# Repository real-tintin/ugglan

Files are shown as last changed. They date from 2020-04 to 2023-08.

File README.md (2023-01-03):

# Ugglan
Ugglan (owl in Swedish) is a hobby drone project. Making use of the
Raspberry Pi Zero 2 W (amongst other things).

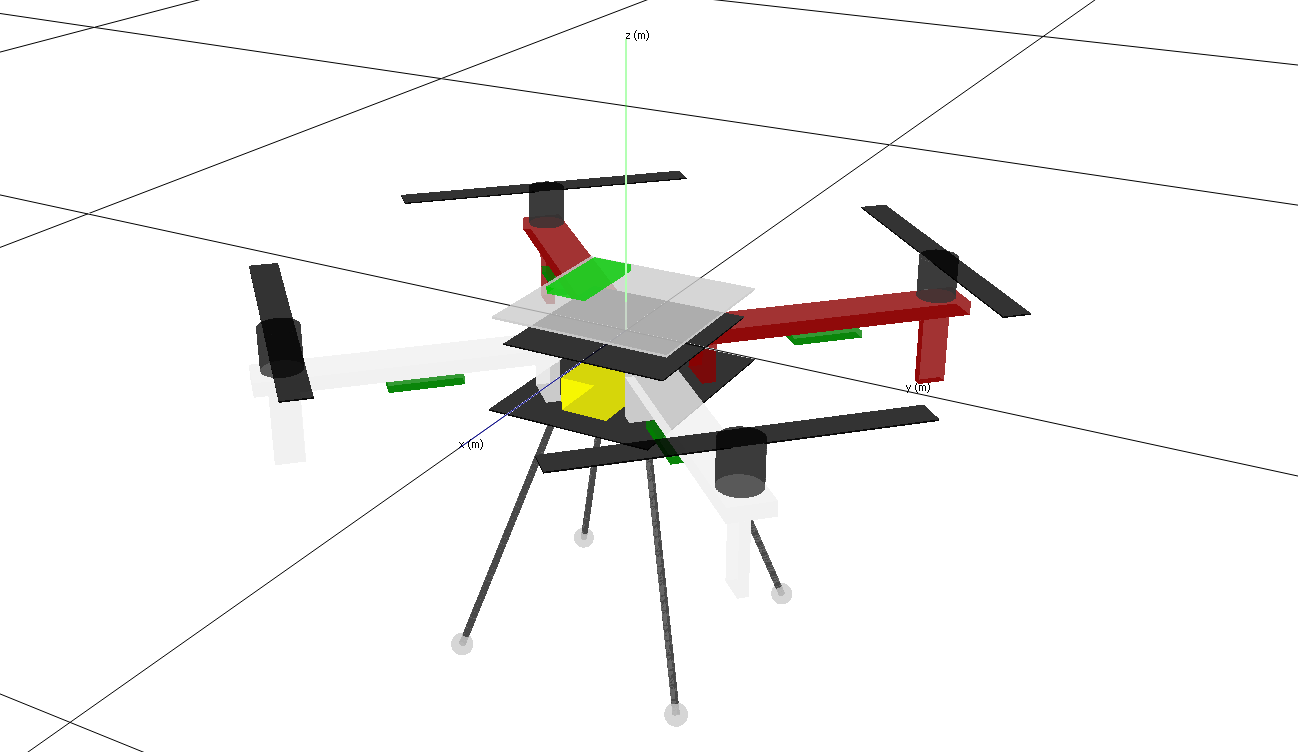
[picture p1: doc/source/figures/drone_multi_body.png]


The project serves as a learning platform for the author himself and
is quite broad, containing everything from assembler to docker. It
also contains some multi body modelling and simulation as well as
state space estimation and control.

## Setup

### Prerequisites
* python >=3.9
* docker
* make

Run the setup script in the root.

```bash
source ./setup.sh
```

## Documentation
[Sphinx](https://www.sphinx-doc.org/en/master/) is used for the generation
of the documentation.

### Build
The documentation is build using `make`.

```bash
make -C ./doc
```

The generated html documentation is found under *./doc/build*.

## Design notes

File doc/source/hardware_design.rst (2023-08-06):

Hardware Design
*****************
.. _ugglan_in_person:
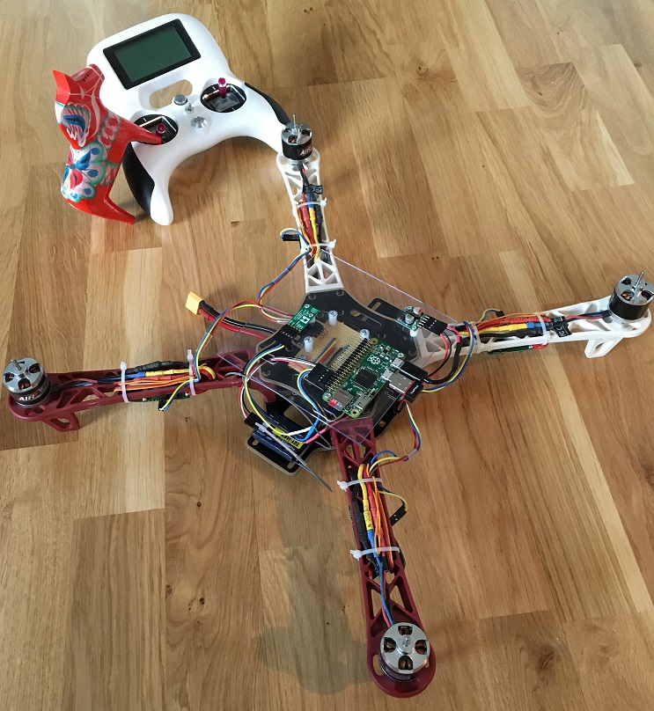
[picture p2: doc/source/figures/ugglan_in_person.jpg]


    Ugglan in person.

Components
==============
The drone hardware components are is listed below

* Raspberry Pi Zero 2 W
* Diatone Q450 with PCB
* Pololu AltIMU-10 v4
* Afro ESC 20 A
* Turnigy Evolution Digital AFHDS 2A RC transmitter & controller
* TGY-iA6C RC receiver
* ZIPPY Compact 3300mAh 3S (or similar)
* DC-DC step down voltage regulator 5V
* T-MOTOR MN2212-V2.0 Brushless Motor (KV920)
* T-MOTOR T9545-A Propeller 9.5x4.5

In addition, miscellaneous self manufactured components such as a cut plexiglas
are used for mounting, see :numref:`ugglan_in_person`.

.. _devices_and_busses:

Devices & Busses
==================
The IMU's and ESC's are communicating with the Pi over i2c. The IMU can run at 400 kHz (fast mode)
and is using the built-in HW. But, the ESC's only run stable at 100 kHz (normal mode) and are
therefore using a SW implementation (i2c-gpio overlay, bit-banging over GPIO 23-24). The RC receiver
is communicating over UART, a serial connection. See overview in :numref:`connected_busses`.

.. _connected_busses:
.. mermaid::
    :caption: Overview of the hardware devices connected to the Pi Zero 2 W and their respective protocols.

    graph TD
        Esc_i -- i2c read 100 kHz --> Raspi
        Raspi -- i2c write 100 kHz --> Esc_i
        Imu_i -- i2c read 400 kHz --> Raspi
        RcReceiver -- uart read 115200 bps --> Raspi

Wiring
==================
.. _wiring_diagram:


    Wiring diagram.

Single core vs. Multi core
============================
During the project, the Raspberry Pi Zero single core processor was upgraded to a 2 W multi core
processor. As the application is utilizing threading, it was interesting to compare the
application performance between the two.

In :numref:`task_exec_rate_single_core` and :numref:`task_exec_rate_multi_core` the task execution
rates in time is shown. As one can see, the execution rates on the multi core processor are much smoother.

.. _task_exec_rate_single_core:


    Task execution rates on the single core Raspberry Pi Zero.

.. _task_exec_rate_multi_core:


    Task execution rates on the multi core Raspberry Pi Zero 2 W.

Vibrations & Attenuation
=========================
The rotating motor with propeller is a source for mechanical vibrations. Un-balanced motors and propellers
will induce vibrations and can cause issue during state estimation e.g., the vibration will propagate thru
the frame to the IMU and cause un-wanted noise.

Motor & Propeller Balancing
^^^^^^^^^^^^^^^^^^^^^^^^^^^^
To reduce vibrations the motor and propeller need to be balanced. To analyze and balance them the IMU acceleration
can be studied. In :numref:`vib_analysis_prop_balancing` the IMU acceleration in time, its variance and psd (power
spectral density) is shown for different runs where a pice of tape is positioned at different locations on a propeller.

.. _vib_analysis_prop_balancing:


    Each chunk corresponds to a separate run of the motors where the pice of tape is relocated. Note,
    chunk 0 is without any tape, chunk 1-3 is tape on one blade and chunk 4-6 on the other blade.

It can be seen that applying tape on a certain location can significantly reduce vibrations i.e., becoming
"better" balanced.

Also note the frequency components of the psd. The content at ~20 Hz could correspond to the frequency of
the motors but folded (due to aliasing as the sample rate 100/2 Hz < 81 Hz, hence at folded at 19 Hz).

Vibration Dampers
^^^^^^^^^^^^^^^^^^
The vibrations experienced by the IMU can be further reduced by installing vibrations dampers between
the frame and the custom mounting plate, see :numref:`ugglan_in_person`.

Different rubber dampers were tested (varying stiffness, mass and size), see :numref:`table_vibration_dampers`
for results.

.. _table_vibration_dampers:

.. table:: * See `data sheet <https://www.tme.eu/Document/3783353bba387d7e09757c85b47027b3/DVA1-3-EN.pdf>`_ for details.

    ====================    ================    ========    ===================     ===================
    Name*                   Stiffness [N/mm]    Mass [g]    Eigenfrequency [Hz]     Variance [m^2/s^4]
    ====================    ================    ========    ===================     ===================
    DVA.1-15-15-M4-10-55    39                  10          314                     1.12
    DVA.1-15-15-M4-10-70    118                 10          537                     0.85
    DVA.1-15-20-M4-10-40    20                  12          206                     2.40
    DVA.1-15-20-M4-10-55    25                  12          230                     1.30
    ====================    ================    ========    ===================     ===================

The above results are rather concise - increasing eigenfrequency will result in less experienced vibrations
by the IMU. This is most likely due the fact that the plate is vibrating about the motor rotational frequency
(~160 Hz). Hence, it would be interesting to test a damper with an eigenfrequency << 160 Hz.

Note, the eigenfrequency is estimated by assuming a classic second order mass-spring system i.e.,
:math:`f_n = \tfrac{1}{2\pi}\sqrt{\tfrac{k}{m}}` (SI-units).

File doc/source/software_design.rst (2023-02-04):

Software Design
*****************

Tasks
=================
The drone's top level software design can be seen as a task manager, (asynchronous
and synchronous) solving the producer and consumer problem. Where the producers are
the sensors (IMU, ESC etc.). And where the control loop, data logging etc. are
the consumers, see :numref:`drone_sw_design`.

.. _drone_sw_design:
.. mermaid::
    :caption: Overview of the drone software design. Tasks are stadium-shaped nodes.

    graph LR
        ImuAccMag([ImuAccMag])
        ImuGyro([ImuGyro])
        ImuPres([ImuPres])

        EscRead([EscRead])
        EscWrite([EscWrite])

        RcReceiver([RcReceiver])

        StateEst([StateEst])
        StateCtrl([StateCtrl])

        DataLogger([DataLogger])

        DataLogQueue[(DataLogQueue)]

        ImuAccMag -- push 100 Hz --> DataLogQueue
        ImuGyro -- push 100 Hz --> DataLogQueue
        ImuPres -- push 10 Hz --> DataLogQueue
        EscRead -- push 1 Hz --> DataLogQueue
        RcReceiver -- push 100 Hz --> DataLogQueue

        DataLogQueue -- last value 100 Hz --> StateEst
        DataLogQueue -- last value 100 Hz --> StateCtrl
        DataLogQueue -- last value 100 Hz --> EscWrite
        DataLogQueue -- last value 100 Hz --> StreamerServer
        DataLogQueue -- pack 10 Hz --> DataLogger

        subgraph Producers
        ImuAccMag
        ImuGyro
        ImuPres
        EscRead
        RcReceiver
        end

        subgraph Consumers
        StateEst
        StateCtrl
        EscWrite
        DataLogger
        StreamerServer
        end

As one can see, the ``DataLogQueue`` maintains a thread safe queue for the producers to
push to and the ``DataLogger`` to pack (pop until empty) from. But it also stores the last
(pushed) sample for consumers to use e.g., the ``StateEst`` which runs at a constant sample
rate i.e., to simplify the signal processing. Note, other tasks than producers may populate
the queue e.g., estimated states which are used by the ``StateCtrl`` or for offline
tuning of control laws.

.. _data_logging:

Data Logging
=================
The ``DataLogger`` handles the data serialization of signals e.g., the IMU acceleration
which is continuously written to disk. It consists of a **HEADER** section - a json string,
describing the content of the second **DATA PACKAGES** section. See :numref:`data_log_protocol`
for an illustration of the data-log protocol.

.. _data_log_protocol:


    The data logging protocol. The **SIGNAL ID** is an unique identifier for each signal/package
    and of type ``uint16``. The **REL TIMESTAMP** is the relative timestamp in ms
    between each **PACKAGE** and of type ``uint8``.

The json-file is compressed using gzip (and base64 encoded) to save space. See example
header below.

.. code-block:: json

    {
        "start_time": "1990-08-30T22:52:50Z",
        "types": {
            "0": "UINT8",
            "1": "UINT16",
            "2": "UINT32",
            "3": "SINT8",
            "4": "SINT16",
            "5": "SINT32",
            "6": "FLOAT",
            "7": "DOUBLE"
        },
        "groups": {
            "0": "IMU",
            "1": "ESC"
        },
        "signals": {
            "0": {
                "name": "AccelerationX",
                "group": 0,
                "type": 7
            },
            "1": {
                "name": "Status0",
                "group": 1,
                "type": 0
            }
        }
    }

State Machine
=================

User Operator
---------------

.. mermaid::
    :caption: User operation of ESC's. LS: Left Switch. MS: Middle Switch.

    stateDiagram

        [*] --> Sound
        Sound --> Disarmed
        Disarmed --> Armed: LS Mid
        Armed --> Disarmed: LS Hi
        Armed --> Alive: LS Lo
        Alive --> Armed: LS Mid
        Disarmed --> [*]: MS Lo

Wireless Streaming
===================
There exists support for wireless data streaming from the drone. The streaming is build
on top of the open-source message library `ZeroMQ <https://zeromq.org>`_. In
:numref:`wireless_streaming_seq_diagram` the communication sequence between the client
(e.g., Laptop) and the server (drone) is illustrated.

.. _wireless_streaming_seq_diagram:
.. mermaid::
    :caption: Communication sequence between the client and the server. Note, only a subset of all available requests are shown.

    sequenceDiagram
        Client->>Server: Request[method: Get_DataLogMetadata<0>, data:{}]
        Server-->>Client: Response[code: Ok<0>, data:<DataLogMetadata as JSON>]
        Client->>Server: Request[method: Set_SelectedDataLogSignals<4>, data:[0,1,2,3]]
        Server-->>Client: Response[code: Ok<0>, data:{}]
        Client->>Server: Request[method: Set_StartStream<2>, data:{}]
        Server-->>Client: Response[code: Ok<0>, data:{}]
        loop
            Server-->>Client: Pushing[Selected data log signal package]
        end
        Client->>Server: Request[method: Set_StopStream<3>, data:{}]
        Server-->>Client: Response[code: Ok, data:{}]

The requests/responses are sent on a socket using the ``REQUEST-REPLY`` pattern, while
the actual selected data log signal bytes are sent on separate socket using the ``PUSH-PULL``
pattern. This to improve performance.

The data sent back and forth via requests/responses are JSON, while the data log signal
package is packed as following::

    <ABS_TIMESTAMP><DATA_LOG_SIGNALS>

and the data log signals are packed as::

    <ID_0><BYTES_0>...<ID_N><BYTES_N>

Note, they are packed somewhat differently compared to the data log signals in
:ref:`data_logging`. This since we can't really unsure that relative timestamps will be
continuous between sent packages.

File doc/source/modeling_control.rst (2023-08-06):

Modeling & Control
*******************
.. _drone_multi_body:


    Multi body analysis of the drone. The 3d model is generated by using
    ``PyQtGraph`` (opengl backend).

Before moving on, note that some in-depth parts of the modeling, state estimation
and Control are not covered in this document, for details see the arthur's master
thesis `Design-Modeling-and-Control-of-an-Octocopter`_.

.. _Design-Modeling-and-Control-of-an-Octocopter: http://www.diva-portal.org/smash/get/diva2:857660/FULLTEXT01.pdf

Nomenclature
===================
:math:`_{I}` Inertial reference frame

:math:`_{B}` Body reference frame

:math:`\tau` Time-constant

:math:`M` Torque

:math:`F` Force

Inertia
===================

Multi Body Modeling
---------------------
Using multi body analysis of the drone and its components, the total drone
(mass and moments) inertia is estimated, see :numref:`drone_multi_body`.
This results in the following inertia estimates

.. math::

    I_{est} =
    \begin{bmatrix}
        0.013 & 0 & 0 \\
        0 & 0.013 & 0 \\
        0 & 0 & 0.024
    \end{bmatrix} \text{kgm}^2

and :math:`m_{est}=1.027` kg. For comparison, the measured weight is :math:`m_{meas}=1.071` kg.
Also its center of mass w.r.t the top frame is located at :math:`CM_{est}=[0, -0.001, -0.011]` m.
Hence, a rather good weight distribution.

The Pendulum Experiment
------------------------
In `Design-Modeling-and-Control-of-an-Octocopter`_ (Section 2.2) an experiment is proposed for
estimation the rotational moment of inertia. This by measuring the period time of a rigid body
rotating about an axis suspended by two strings i.e., bifilar pendulum.

Without going into the details, :math:`I_{zz}` was estimated by suspending the drone by two
strings apart :math:`D=0.46` m with length :math:`L=2.16` m, see :numref:`pendulum_experiment`.

.. _pendulum_experiment:
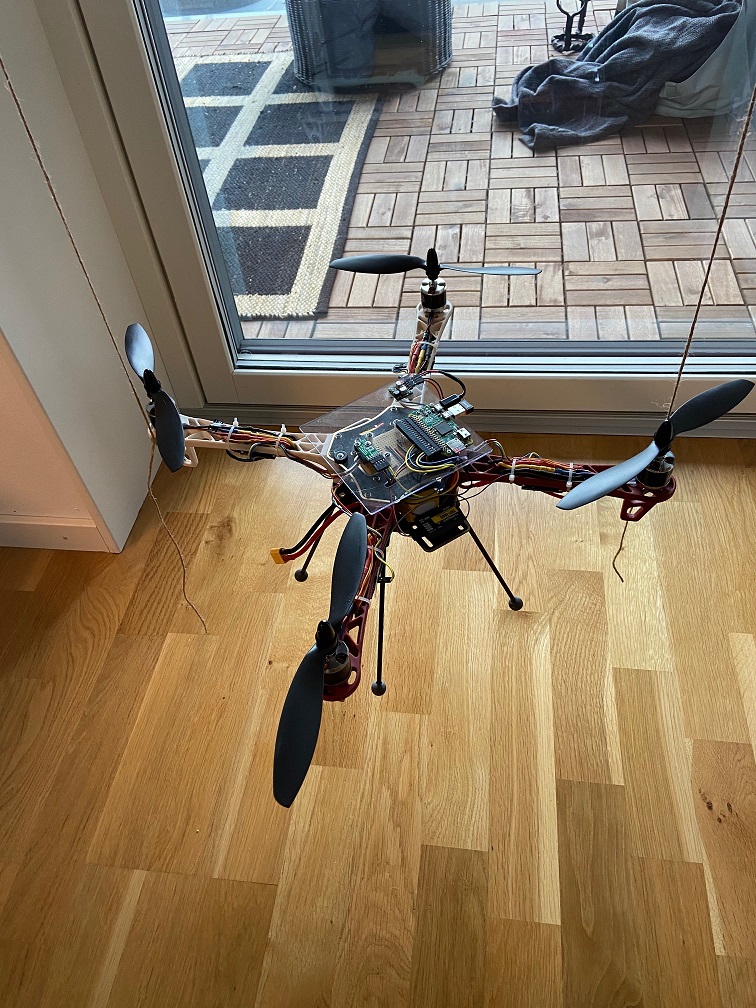
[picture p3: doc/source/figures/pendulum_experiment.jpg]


    Ugglan suspended by two strings - help?!

In total 10 measurements where made of the number of periods and the total time, listed in
:numref:`table_pendulum`.

.. _table_pendulum:

.. table:: :math:`N` number of periods and :math:`t` total time.

    =======  =======
    N        t [s]
    =======  =======
    10       19.3
    10       19.4
    15       29.2
    15       29.1
    20       39.0
    20       38.8
    25       48.2
    25       48.2
    30       58.1
    30       57.8
    =======  =======

Computing the mean period yields :math:`T=1.94` s. This in terms results in
:math:`I_{zz}=0.025 \text{ kgm}^2`. This can be seen as an validation of the estimation
from the multi body modeling.

Motor Dynamics
================
The motor dynamics, :math:`u_{M_i}\rightarrow\omega_{M_iz}` are modelled as a simple first order
LTL system (low-pass filter)

.. math::

    \Omega_{M_iz}(s) = \frac{1}{\tau_M s + 1}U_{M_i}(s)

where :math:`\tau_M` is the motor time constant. The time constant can be estimated by analyzing
the systems step response. By assuming :math:`\omega_{M_i}(0) = u_0` and
:math:`\omega_{M_i}(\infty) = u_\infty`, before and after the step response as settled, one gets

.. math::

    \omega_{M_i}(t) = u_\infty + (u_0 - u_\infty) e^{\frac{-t}{\tau_M}}

which can be re-written as

.. math::

    \ln\left(\frac{u_\infty - u_0}{u_\infty - \omega_{M_i}(t)}\right) = \tau_M^{-1} t

assuming :math:`u_\infty > u_0`. By then measuring :math:`\omega_{M_i}` and :math:`t` one can
estimate :math:`\tau_M` by using least squares regression. Note the data points for the regression
should be selected such that the problem is well conditioned i.e.,
:math:`\omega_{M_i} \lesssim u_\infty`.

In :numref:`tau_motor_dynamics` the time constant is estimated. One can see that it does vary
and decrease with an increasing :math:`u_0`, introducing a non-linearity. Moreover,
:math:`\tau_M` varies for positive and negative steps.

The seen effects have to be neglected to keep linearity. Therefore, the resulting time constant
is given by the mean of the steps responses where :math:`\omega_M \in [400, 800]` i.e., within
normal operating conditions. This gives :math:`\tau_M = 0.08`.

.. _tau_motor_dynamics:


    Positive and negative motor step responses (with mounted propeller). The time constant
    is estimated for each step using MLSE.

On a further note. The approximation of using a first order low pass filter is fine. But from the
figure it becomes clear that better approximations of higher order exist. An improvement would
be to empirical derive such a system - by using system identification.

Linearized State Space
=======================
The same linearized (SIMO) state-space representation as derived in
`Design-Modeling-and-Control-of-an-Octocopter`_ (Section 3.7) is used i.e.,

.. math::

    \mathbf{\dot{x}_i} &= \mathbf{A_i x_i} + \mathbf{B_i} u_i \\
    \mathbf{y_i} &= \mathbf{C_i x_i} + \mathbf{D_i} u_i, i = 1,2,...,6

where :math:`\mathbf{x_i}\in\mathbb{R}^3`, :math:`\mathbf{y_i}\in\mathbb{R}^2` and

.. math::
    :label: state_space_matrices

    \mathbf{A_i}=
    \begin{bmatrix}
        0 & 1 & 0 \\
        0 & 0 & 1 \\
        0 & 0 & -\tfrac{1}{\tau_M}
    \end{bmatrix},
    \mathbf{B_i}=
    \begin{bmatrix}
        0 \\
        0 \\
        \tfrac{c_i}{\tau_M}
    \end{bmatrix},
    \mathbf{C_i}=
    \begin{bmatrix}
        1 & 0 & 0 \\
        0 & 1 & 0 \\
        0 & 0 & 1
    \end{bmatrix},
    \mathbf{D_i}= 0.

Here :math:`\mathbf{c} = [\tfrac{1}{m}, \tfrac{1}{m}, \tfrac{1}{m}, \tfrac{1}{I_{xx}},
\tfrac{1}{I_{yy}}, \tfrac{1}{I_{zz}}]`. For instance :math:`i = 4` corresponds to the
state-space representation in roll

.. math::

    \mathbf{x_4}=
    \begin{bmatrix}
        \phi \\
        \dot\phi \\
        \ddot\phi \\
    \end{bmatrix},
    u_4=u_\phi,
    c_4=\tfrac{1}{I_{xx}}.

Note, the final state e.g., :math:`\ddot\phi` is estimated using a Kalman filter,
see :ref:`attitude-estimation`. This differs from the master thesis, where it was
estimated using a reduced observer.

State Estimation
=================

.. _attitude-estimation:

Attitude Estimation
--------------------
For attitude control, the Euler angles :math:`\eta = [\phi, \theta, \psi]` and their respective
time derivatives :math:`\dot{\eta}` (angular rates) and :math:`\ddot{\eta}` (angular accelerations)
are needed.

Geometry of IMU
^^^^^^^^^^^^^^^^
The euler angles can directly be computed from the IMU's accelerometer and magnetometer using
the geometrical relationships

.. math::

    \phi_{acc} &= \text{atan2}(-a_{By}, -a_{Bz}) \\
    \theta_{acc} &= \text{atan2}(a_{Bx}, \sqrt{a_{By}^2 + a_{Bz}^2}) \\
    \psi_{mag} &= \text{atan2}(-B_{Iy}, B_{Ix})

where

.. math::

    B_{Ix} &= B_{Bx}\cos(\theta) + B_{By}\sin(\phi)\sin(\theta) + B_{Bz}\sin(\theta)\cos(\phi) \\
    B_{Iy} &= B_{By}\cos(\phi) - B_{Bz}\sin(\phi)

and :math:`a_B` is the acceleration and :math:`B_B` is the earths magnetic field supplied by the
IMU in the body frame. Where :math:`B_{Ix}` and :math:`B_{Iy}` are the magnetic fields in the
inertial frame.

However, the estimates are noisy (see :numref:`ang_est`) and need to be enhanced
e.g., by filtering.

Kalman Filter
^^^^^^^^^^^^^^
A full state attitude estimation can be accomplished by using a Kalman filter (MLSE filter which assumes
linearity and Gaussian noise) see e.g., `Wikipedia <https://en.wikipedia.org/wiki/Kalman_filter>`_ for
details. This is a rather common approach for attitude estimation given the IMU outputs. So, without
going into the details, the time discretized state space model in this case becomes

.. math::
    :label: kalman_filter_ss

    \mathbf{F}=
    \begin{bmatrix}
        1 & \Delta t & \tfrac{\Delta t^2}{2} \\
        0 & 1 & \Delta t \\
        0 & 0 & 1
    \end{bmatrix},
    \mathbf{B}= 0,
    \mathbf{H}=
    \begin{bmatrix}
        1 & 0 & 0 \\
        0 & 1 & 0
    \end{bmatrix}

with the selected covariance matrices

.. math::
    :label: kalman_filter_cov

    \mathbf{Q}= \kappa_{Q}
    \begin{bmatrix}
        \tfrac{\Delta t^4}{4} & \tfrac{\Delta t^3}{2} & \tfrac{\Delta t^2}{2} \\
        \tfrac{\Delta t^3}{2} & \Delta t^2 & \Delta t \\
        \tfrac{\Delta t^2}{2} & \Delta t & 1
    \end{bmatrix},
    \mathbf{R}=
    \begin{bmatrix}
        \kappa_{R_0} & 0 \\
        0 & \kappa_{R_1}
    \end{bmatrix},
    \mathbf{P}_0= I.

The :math:`\kappa` are tunable parameters of the filter.

See :ref:`estimator-performance` for the final performance
and comparison w.r.t to other filtering methods.

Complementary filter
^^^^^^^^^^^^^^^^^^^^^
Another method to improve the (angle only) estimates is to use a first order complementary filter -
fusing the accelerometer angles with the integrated gyro estimates (see
`IMU Data Fusing <http://www.olliw.eu/2013/imu-data-fusing/>`_)

.. math::

    \tilde{\phi}^{k} &= \text{cf}(\phi_{acc}^k, \dot{\phi}_{gyro}^k, \tilde{\phi}^{k-1}, \tau_{\phi}) \\
    \tilde{\theta}^{k} &= \text{cf}(\theta_{acc}^k, \dot{\theta}_{gyro}^k, \tilde{\theta}^{k-1}, \tau_{\theta}) \\
    \tilde{\psi}^{k} &= \text{cf}(\psi_{mag}^k, \dot{\psi}_{gyro}^k, \tilde{\psi}^{k-1}, \tau_{\psi})

where

.. math::

    y^{k} &= \text{cf}(u^k, \dot{u}^k, y^{k-1}, \tau) \\
            &= \alpha(y^{k-1} + \dot{u}^k\Delta t) + (1-\alpha)u^k

where :math:`\alpha = \tfrac{\tau}{\tau + \Delta t}` and :math:`\tau` is the cut-off frequency
(:math:`\tau = \tfrac{1}{2 \pi f_c}`).

.. _estimator-performance:

Estimator Performance
^^^^^^^^^^^^^^^^^^^^^^
In :numref:`ang_est` - :numref:`ang_acc_est` the final performance of the attitude
estimation is show for different estimators.

.. _ang_est:


    Angle estimation using the IMU (accelerometer + magnetometer), integrated gyro,
    complementary filter and the Kalman filter.

.. _ang_rate_est:


    Angular rate estimation using the gyro output and the Kalman filter.

.. _ang_acc_est:


    Angular acceleration estimation using the derivative of the gyro (w/o a LP-filter)
    and the Kalman filter.

Implementation Notes
^^^^^^^^^^^^^^^^^^^^^

Kalman Filter
"""""""""""""""""
In order to solve for the optimal Kalman gain, matrix operations (e.g., inverse) have
to be performed. For this `Eigen <https://eigen.tuxfamily.org/>`_ is used.

Range Limit
"""""""""""""""
The estimates need to be range limited i.e., modulo of the euler angles e.g.,
:math:`\theta \in [-\pi, \pi]`.

Accelerometer Static Errors
"""""""""""""""""""""""""""
The accelerometer output is typically polluted with static errors which need
to be compensated for. These errors can split into scaling errors, misalignment
errors and biases (offset errors). The relation between the raw sensor output
:math:`\tilde{V}` and the true (compensated) output :math:`V` can be expressed
as following

.. math::

    \underbrace{
        \begin{bmatrix}
            x \\
            y \\
            z
        \end{bmatrix}
    }_V =
    \underbrace{
        \begin{bmatrix}
            s_x & 0 & 0 \\
            0 & s_y & 0 \\
            0 & 0 & s_z
        \end{bmatrix}
    }_S
    \underbrace{
        \begin{bmatrix}
                1 & m_{xy} & m_{xz} \\
                m_{yx} & 1 & m_{yz} \\
                m_{zx} & m_{zy} & 1
        \end{bmatrix}
    }_M
    \underbrace{
        \begin{bmatrix}
            \tilde{x} \\
            \tilde{y} \\
            \tilde{z}
        \end{bmatrix}
    }_\tilde{V} -
    \underbrace{
        \begin{bmatrix}
                b_x \\
                b_y \\
                b_z
        \end{bmatrix}
    }_B.

The matrices :math:`S`, :math:`M` and :math:`B` can be estimated
by using least squares regression of measurements where the expected
output is known.

Below in :numref:`acc-static-errors` the residuals of a regression of
six different measurements is shown. Where each axis is aligned with
the gravity, in both the positive and the negative direction.

.. _acc-static-errors:


    MLSE residuals of accelerometer statical error estimation.

One can see that the fitted model doesn't manage to remove all errors.
There might exist non-linearities left to model.

Gyro Bias
""""""""""
The gyro output contains an bias which needs to be compensated for. This
can be estimated dynamically during the standstill of the drone.

Hard Iron Bias
"""""""""""""""
Magnetic fields affecting the magnetometer other than earth's need to be compensated
for. One of those is hard iron (the other being soft iron) effects. These are static
magnetic fields e.g., components on the PCB.

These biases can easily be estimated using least squares (offset of a sphere)

.. math::

    \underset{V}{\text{minimize}} (B-V)^T (B-V) = B^2.

To get a good estimate, the magnetometer should be rotated in space to excite all
directions, see :numref:`hard_iron_bias`.

.. _hard_iron_bias:


    Hard iron bias estimation and correction.

State Control
=================
The drone's dynamics are stabilized using a full state feedback controller

.. math::
    :label: cont_state_feedback

    u = -\mathbf{Lx}.

Which allows for arbitrary pole placement, see `Design-Modeling-and-Control-of-an-Octocopter`_
for in depth details.

Pilot Control
---------------------
Typically, the pilot controller (using the handheld controller), seeks for stability
of roll, pitch and yaw-rate. To tune :math:`\mathbf{L}`, the step response of the
linearized closed-loop system can be analyzed, see :numref:`tune_ctrl_roll_pitch`-
:numref:`tune_ctrl_yaw_rate`. Note, an integrated state has been added for roll
and pitch control (already in place for yaw-rate) i.e., :math:`\mathbf{x}\in\mathbb{R}^4`.

.. _tune_ctrl_roll_pitch:


    Tuning and parameter selection for roll and pitch control.

.. _tune_ctrl_yaw_rate:


    Tuning and parameter selection for yaw-rate control.

In the above figures the abs-max value of the integrated state (reference error)
is also shown to determine a suitable value for anti-windup i.e., to handle a
large overshoot/instability caused by the integration.

In :numref:`rc_gimbal_def_pilot` the RC-gimbal definitions for the pilot controller
are given.

.. _rc_gimbal_def_pilot:


    RC-gimbal definitions for the pilot controller. The arrow indicates
    positive direction. Note that thrust implies negative :math:`F_z` i.e., lift.

Motor Control
=================
The body force and torque control inputs :math:`u_{Bz}`, :math:`u_{B\phi}`,
:math:`u_{B\theta}` and :math:`u_{B\psi}` have to be converted to individual
motor control inputs :math:`u_{M_i}`.

.. _motor_rotations:


    The drone motor rotational directions.

From :numref:`motor_rotations` one can derive the drone body forces and
torques generated by the motors

.. math::

    F_{Bx} &= 0 \\
    F_{By} &= 0 \\
    F_{Bz} &= - F_{M_1z} - F_{M_2} - F_{M_3} - F_{M_4z} \\
    M_{Bx} &= - l_xF_{M_1z} - l_xF_{M_2z} + l_xF_{M_3z} + l_xF_{M_4z} \\
    M_{By} &=   l_xF_{M_1z} - l_xF_{M_2z} - l_xF_{M_3z} + l_xF_{M_4z} \\
    M_{Bz} &= - M_{M_1z} + M_{M_2z} - M_{M_3z} + M_{M_4z}

where :math:`F_{M_ix} = F_{M_iy} = M_{M_ix} = M_{M_iy} = 0` and
:math:`l_x = 0.23` m (distance between body center of mass and motor).

In order to solve for the motor inputs one can use the fact that
:math:`F, M \propto \omega^2`, where :math:`\omega` is the angular rate of a
motor/propeller, see :numref:`ang_rate_sq_vs_thrust`.

.. _ang_rate_sq_vs_thrust:


    Motor angular rate and its corresponding generated thrust. Positive
    rotation corresponds to the "intended" propeller rotation i.e., not
    driven in reverse. Fitted a 1st-order polynomial :math:`y = X[p_1]^\intercal`.

Hence, the generated body forces and torques can be described as following

.. math::

    \begin{bmatrix}
        F_{Bz} \\
        M_{Bx} \\
        M_{By} \\
        M_{Bz}
    \end{bmatrix} =
    \underbrace{
        \begin{bmatrix}
            -c_{Fz} & -c_{Fz} & -c_{Fz} & -c_{Fz} \\
            -l_xc_{Fz} & -l_xc_{Fz} & l_xc_{Fz} & l_xc_{Fz} \\
            l_xc_{Fz} & -l_xc_{Fz} & -l_xc_{Fz} & l_xc_{Fz} \\
            -c_{Mz} & c_{Mz} & -c_{Mz} & c_{Mz}
        \end{bmatrix}
    }_H
    \begin{bmatrix}
        \omega_{M_1z}^2 \\
        \omega_{M_2z}^2 \\
        \omega_{M_3z}^2 \\
        \omega_{M_4z}^2
    \end{bmatrix}.

By computing :math:`H^{-1}` one gets

.. math::

    [\omega_{M_1z}^2, \omega_{M_2z}^2, \omega_{M_3z}^2, \omega_{M_4z}^2]^\intercal
    = H^{-1} [F_{Bz}, M_{Bx}, M_{By}, M_{Bz}]^\intercal

where

.. math::
    H^{-1} = \frac{1}{4}
        \begin{bmatrix}
            -\tfrac{1}{c_{Fz}} & -\tfrac{1}{l_xc_{Fz}} & \tfrac{1}{l_xc_{Fz}} & -\tfrac{1}{c_{Mz}} \\
            -\tfrac{1}{c_{Fz}} & -\tfrac{1}{l_xc_{Fz}} & -\tfrac{1}{l_xc_{Fz}} & \tfrac{1}{c_{Mz}} \\
            -\tfrac{1}{c_{Fz}} & \tfrac{1}{l_xc_{Fz}} & -\tfrac{1}{l_xc_{Fz}} & -\tfrac{1}{c_{Mz}} \\
            -\tfrac{1}{c_{Fz}} & \tfrac{1}{l_xc_{Fz}} & \tfrac{1}{l_xc_{Fz}} & \tfrac{1}{c_{Mz}}
        \end{bmatrix}.

From :numref:`ang_rate_sq_vs_thrust` it can be seen that :math:`c_{Fz}` is smaller (about half)
when the motor is reversing (negative rotation). This is probably due to the non-symmetrical
shape of the propeller. Hence, a non-linearity arises and :math:`H^{-1}` can't solely be used.
Therefore reversing will for now not be used, maybe in the future.

Anyhow, :numref:`ang_rate_sq_vs_thrust` also gives :math:`c_{Fz} = -7.10\times 10^{-6}` (positive rotation
from now on only). The torque constant is given by :math:`c_{Mz} = \tfrac{1}{50} c_{Fz}` - empirical
relation from the master thesis.

In :numref:`ang_rate_vs_command` the empirical relation between the raw motor
control inputs and the angular rates is given.

.. _ang_rate_vs_command:


    The motor angular rates and raw control inputs. Fitted a 1nd-order polynomial
    :math:`y = X[p_1, p_0]^\intercal`. Note, first 5 values are not included in the
    regression for a better fit - not a commonly used interval. Also note the
    symmetry about :math:`u`.

Hence, the final conversion is given by

.. math::
    u_{M_i} =
    \begin{cases}
        45\omega_{M_iz} - 6656 & \text{if } \omega_{M_iz} \geq 200 \\
        0 & \text{otherwise}
    \end{cases}.

Note, :math:`u_{M_i}` should also be range limited since is it a ``int16`` and reversing
is not used.

Simulation
=================
The full non-linear 6-dof (degrees of freedom) model derived in
`Design-Modeling-and-Control-of-an-Octocopter`_ is implemented and packaged in a simulator
and made available via a gui, see :numref:`gui_6dof_sim`. Summary of the simulation model:

* Non-linear 6-dof rigid body model (using quaternions)
* Modelling of the drone body forces and torques e.g., drag, persistance and motor dynamics
* Modelling of the IMU (with sensor noise)
* Integrated attitude estimator (Kalman filter)
* Integrated state feedback controller

With the gui, it becomes effortless to test and tune e.g., the control laws or the
Kalman filter. The model, estimator, controller etc. are configurable via the gui.

The simulation runs in real-time and the the reference inputs can either be given as a
step response or by using a gamepad. Multiple pre-defined subplots (widgets) can be
selected and shown.

.. _gui_6dof_sim:
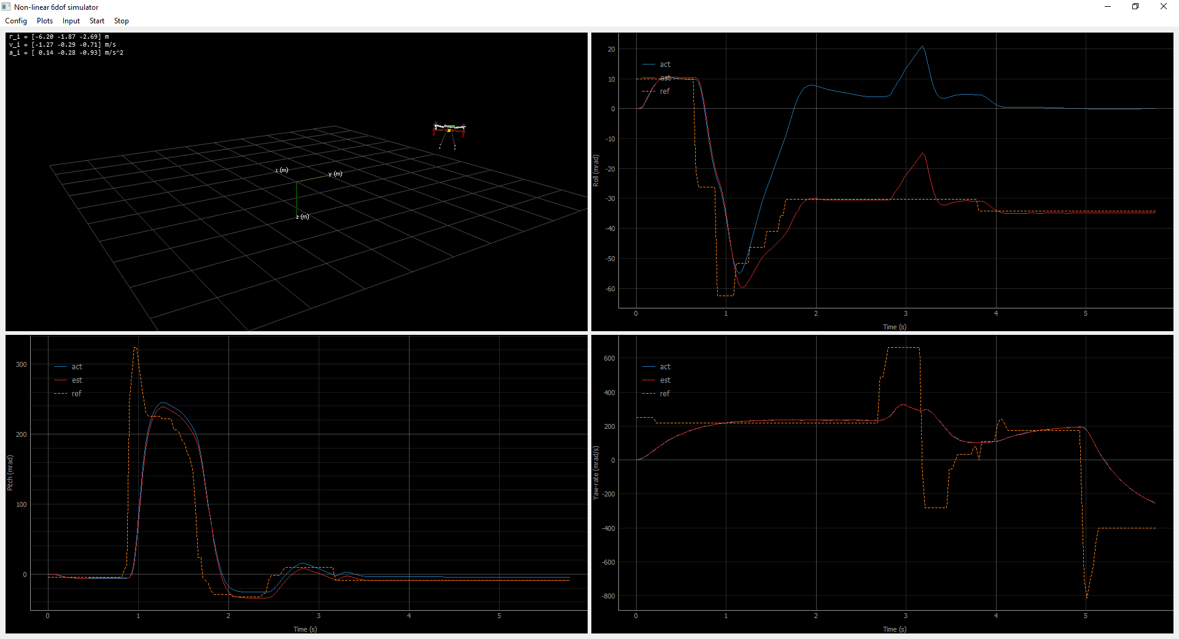
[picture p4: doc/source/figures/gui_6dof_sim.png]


    Non-linear 6-dof simulator gui, implemented using ``PyQtGraph``.

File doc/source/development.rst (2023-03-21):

Development
*****************
Test driven development is emphasized in this project.

.. _py_unit_testing:

Python Unit Testing
====================
The unit test framework ``pytest`` is used for unit testing of the Python
code (mainly used for tools). To execute all tests (and build pkg)::

    make -C ./tools -f Makefile

C++ Unit Testing
=================
The drone core is written in C++. To test and verify its functionality,
the test framework `Catch 2 <https://github.com/catchorg/Catch2>`_ is used.

To run all unit tests in docker::

    make -C ./raspi -f Makefile_tests

C++ Debugging
==============
To build the C++ application for debug::

    make -C ./raspi -f Makefile_tests build_tests_for_debug

This will produce debugging information for ``gdb``. Hence, install
gdb and debug the built binary::

    apt-get install gdb
    gdb path/to/binary

Note, this requires a setup of the env, see *raspi/Dockerfile* and
*raspi/Makefile_tests*.

For convince one can run and debug in the ``raspi`` Docker container.
Attache VS code to the running instance for an IDE.

ESC Compile & Flash
=====================
The drone uses the Afro ESC (Electronic Speed Controllers) to control the
brushless motors. They allow for communication via i2c and motor feedback such
as its angular-rate, temperature and voltage.

In order to enable the i2c feedback and update its address, the onboard Atmel AVR
Atmega8 have to be re-flashed. For flashing, the `Afro ESC USB programming tool <https://hobbyking.com/en_us/afro-esc-usb-programming-tool.html>`_
as well as the `USBasp programer for Atmel AVR controllers <https://www.fischl.de/usbasp/>`_
can be used. Note, the Afro USB programmer only works if the ESC has been pre-flashed
with the bootloader for PWM flashing.

To compile setup ``avra`` (https://github.com/Ro5bert/avra) and for flashing
``avrdude`` (http://savannah.nongnu.org/projects/avrdude). BlueRobotics have
manipulated the ESC source code and enabled for i2c feedback. Their Git repo has
been forked e.g., use Git submodules::

    git submodule add https://github.com/real-tintin/tgy

For simplified compiling and flashing, use the included `makefile` or the
`KKMulitCopter GUI <https://lazyzero.de/en/modellbau/kkmulticopterflashtool>`_.

Note, to change the default rotation direction, modify ``MOTOR_REVERSE`` in *tgy.asm*.

Setup Env on Target
====================
Todo's before deploying on target (Raspbian).

External devices
----------------
In :ref:`devices_and_busses` the external devices and busses are discussed. To enabled and
configure the needed pins on the Pi, add the following to the end of ``/boot/config.txt``::

    # Enable HW i2c in fast mode (400 kHz)
    dtparam=i2c=on
    dtparam=i2c_baudrate=400000

    # Enable SW i2c in normal mode (100 kHz)
    dtoverlay=i2c-gpio,bus=4,i2c_gpio_delay_us=2,i2c_gpio_sda=23,i2c_gpio_scl=24

    # Enable UART
    enable_uart=1

Note, if the GPIO serial pins are used, verify that the login prompt on ``/dev/serial0`` is
disable. If not, there might be another process (getty), reading from the same port,
causing issues. This can be configured via ``raspi-config``.

Remote access
--------------
Setup ssh and network interfaces for remote access e.g., connecting to a hotspot.

Build for & Deploy on Target
=============================
To build for target, the source is cross compiled in a Raspbian Docker container::

    make -C ./raspi -f Makefile_dpkg

It is also possible to compile for profiling::

    make -C ./raspi -f Makefile_dpkg build_dpkg_for_profiling

A profiling report can be generated using ``gprof``, see
`What is gprof? <https://users.cs.duke.edu/~ola/courses/programming/gprof.html>`_.

This will also build a Debian package (``ugglan.deb``) which can easily be deployed on
target by using::

    dpkg --install path/to/ugglan.deb

Tools
======
For development various tools are made available e.g., tuning of the state
controller. These are written in Python and bundled in a package. To install
locally::

    pip install -e ./tools/

Beside the possibility to importing and use the modules, some useful cli's
(console scripts) are made available e.g., plotting and analysis of a data
log file::

    plot-data-log path/to/file.dat

To explicitly add new minimally required dependencies, update ``install_requires``
in the ``setup.py``.

Python Requirements
====================
When new Python packages are needed and installed, the ``requirements.txt`` shall be
updated accordingly. Under python virtual env::

    py -m pip freeze > requirements.txt

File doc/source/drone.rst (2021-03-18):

Drone
*****************
The drone a.k.a "Ugglan" (Swedish for owl) is a DIY build
quadcopter, using the Raspberry Pi Zero.

Some in-depth parts of the Modeling, State Estimation and Control
are not covered in this document, for details see the arthur's master thesis
`Design-Modeling-and-Control-of-an-Octocopter`_.

.. _Design-Modeling-and-Control-of-an-Octocopter: http://www.diva-portal.org/smash/get/diva2:857660/FULLTEXT01.pdf

Software
=================

Tasks
---------------
The drone's top level software design can be seen as a task manager, (asynchronous
and synchronous) solving the producer and consumer problem. Where the producers are
the sensors (IMU, ESC etc.). And where the control loop, data logging etc. are
the consumers, see :numref:`drone_sw_design`.

.. _drone_sw_design:
.. mermaid::
    :caption: Overview of the drone software design. Tasks are stadium-shaped nodes.

    graph LR
        ImuAccMag([ImuAccMag])
        ImuGyro([ImuGyro])
        ImuPres([ImuPres])

        EscRead([EscRead])
        RcReceiver([RcReceiver])

        DataLogQueue[(DataLogQueue)]

        StateControl([StateControl])
        EscWrite([EscWrite])
        DataLogger([DataLogger])

        ImuAccMag -- push 50 Hz --> DataLogQueue
        ImuGyro -- push 50 Hz --> DataLogQueue
        ImuPres -- push 12.5 Hz --> DataLogQueue
        EscRead -- push 5 Hz --> DataLogQueue
        RcReceiver -- push 50 Hz --> DataLogQueue

        DataLogQueue -- last value 50 Hz --> StateControl
        DataLogQueue -- last value 50 Hz --> EscWrite
        DataLogQueue -- pop 100 Hz --> DataLogger

        subgraph Producers
        ImuAccMag
        ImuGyro
        ImuPres
        EscRead
        RcReceiver
        end

        subgraph Consumers
        StateControl
        EscWrite
        DataLogger
        end

As one can see, the ``DataLogQueue`` maintains a thread safe queue for the producers to
push to and the ``DataLogger`` to pop from. But it also stores the last (pushed) sample
for consumers to use e.g., the ``StateControl`` which runs at a constant execution/sample
rate i.e., to simplify the signal processing. Note, other tasks than producers may populate
the queue e.g., estimated states which are useful for offline tuning of control laws.

Note, some signals such as the ones from the pressure sensor will only be sampled
at 12.5 Hz. This has to be handled by the state controller.

Data Logging
-----------------
The ``DataLogger`` handles the data serialization of signals e.g., the IMU acceleration
which is continuously written to disk. It consists of a **HEADER** section - a json string,
describing the content of the second **DATA PACKAGES** section. See :numref:`data_log_protocol`
for an illustration of the data-log protocol.

.. _data_log_protocol:


    The data logging protocol. The **SIGNAL ID** is an unique identifer for each signal/package
    and of type ``uint16``. The **REL TIMESTAMP** is the relative timestamp in ms
    between each **PACKAGE** and of type ``uint8``.

The json-file is compressed using gzip (and base64 encoded) to save space. See example
header below.

.. code-block:: json

    {
        "start_time": "1990-08-30T22:52:50Z",
        "types": {
            "0": "UINT8",
            "1": "UINT16",
            "2": "UINT32",
            "3": "SINT8",
            "4": "SINT16",
            "5": "SINT32",
            "6": "FLOAT",
            "7": "DOUBLE"
        },
        "groups": {
            "0": "IMU",
            "1": "ESC"
        },
        "signals": {
            "0": {
                "name": "AccelerationX",
                "group": 0,
                "type": 7
            },
            "1": {
                "name": "Status0",
                "group": 1,
                "type": 0
            }
        }
    }

State Machine
---------------

User Operator
^^^^^^^^^^^^^

.. mermaid::
    :caption: User operation of ESC's. LS: Left Switch. MS: Middle Switch.

    stateDiagram

        [*] --> Sound
        Sound --> Disarmed
        Disarmed --> Armed: LS Mid
        Armed --> Disarmed: LS Hi
        Armed --> Alive: LS Lo
        Alive --> Armed: LS Mid
        Disarmed --> [*]: MS Lo

Hardware
=================
.. _ugglan_in_person:


    Ugglan in person.

The drone hardware components are is listed below

* Raspberry Pi Zero
* Diatone Q450 with PCB
* Pololu AltIMU-10 v4
* Afro ESC 20 A
* Turnigy Evolution Digital AFHDS 2A RC transmitter & controller
* TGY-iA6C RC receiver
* ZIPPY Compact 3300mAh 3S (or similar)
* DC-DC step down voltage regulator 5V
* Turnigy 2830 900KV L2215J-900 Brushless Motor

In addition, miscellaneous self manufactured components such as a cut plexiglas
are used for mounting, see :numref:`ugglan_in_person`.

.. _devices_and_busses:

Devices & Busses
-----------------
The IMU's and ESC's are communicating with the Pi over i2c. The IMU can run at 400 kHz (fast mode)
and is using the built-in HW. But, the ESC's only run stable at 100 kHz (normal mode) and are
therefore using a SW implementation (i2c-gpio overlay, bit-banging over GPIO 23-24). The RC receiver
is communicating over UART, a serial connection. See overview in :numref:`connected_busses`.

.. _connected_busses:
.. mermaid::
    :caption: Overview of the hardware devices connected to the Pi Zero and their respective protocols.

    graph TD
        Esc_i -- i2c read 100 kHz --> Raspi
        Raspi -- i2c write 100 kHz --> Esc_i
        Imu_i -- i2c read 400 kHz --> Raspi
        RcReceiver -- uart read 115200 bps --> Raspi

Wiring
--------
.. _wiring_diagram:


    Wiring diagram.

Modeling
===============

.. _drone_multi_body:


    Multi body analysis of the drone.

Nomenclature
------------------
:math:`_{I}` Inertial reference frame

:math:`_{B}` Body reference frame

:math:`\tau` Time-constant

:math:`M` Torque

:math:`F` Force

Inertia
------------------

Multi Body Modeling
^^^^^^^^^^^^^^^^^^^^
Using multi body analysis of the drone and its components, the total drone
(mass and moments) inertia is estimated, see :numref:`drone_multi_body`.
This results in the following inertia estimates

.. math::

    I_{est} =
    \begin{bmatrix}
        0.014 & 0 & 0 \\
        0 & 0.014 & 0 \\
        0 & 0 & 0.026
    \end{bmatrix} \text{kgm}^2

and :math:`m_{est}=1.071` kg. For comparison, the measured weight is :math:`m_{meas}=1.096` kg.
Also its center of mass w.r.t the top frame is located at :math:`CM_{est}=[0, -0.001, -0.009]` m.
Hence, a rather good weight distribution.

The Pendulum Experiment
^^^^^^^^^^^^^^^^^^^^^^^^
In `Design-Modeling-and-Control-of-an-Octocopter`_ (Section 2.2) an experiment is proposed for
estimation the rotational moment of inertia. This by measuring the period time of a rigid body
rotating about an axis suspended by two strings i.e., bifilar pendulum.

Without going into the details, :math:`I_{zz}` was estimated by suspending the drone by two
strings apart :math:`D=0.46` m with length :math:`L=2.16` m, see :numref:`pendulum_experiment`.

.. _pendulum_experiment:


    Ugglan suspended by two strings - help?!

In total 10 measurements where made of the number of periods and the total time, listed in
:numref:`table_pendulum`.

.. _table_pendulum:

.. table:: :math:`N` number of periods and :math:`t` total time.

    =======  =======
    N        t [s]
    =======  =======
    10       19.3
    10       19.4
    15       29.2
    15       29.1
    20       39.0
    20       38.8
    25       48.2
    25       48.2
    30       58.1
    30       57.8
    =======  =======

Computing the mean period yields :math:`T=1.94` s. This in terms results in
:math:`I_{zz}=0.025 \text{ kgm}^2`. This can be seen as an validation of the estimation
from the multi body modeling.

Motor Dynamics
------------------
The motor dynamics, :math:`u_{M_i}\rightarrow\omega_{M_iz}` are modelled as a simple first order
LTL system (low-pass filter)

.. math::

    \Omega_{M_iz}(s) = \frac{1}{\tau_M s + 1}U_{M_i}(s)

where :math:`\tau_M` is the motor time constant. The time constant can be estimated by analyzing
the systems step response. By assuming :math:`\omega_{M_i}(0) = u_0` and
:math:`\omega_{M_i}(\infty) = u_\infty`, before and after the step response as settled, one gets

.. math::

    \omega_{M_i}(t) = u_\infty + (u_0 - u_\infty) e^{\frac{-t}{\tau_M}}

which can be re-written as

.. math::

    \ln\left(\frac{u_\infty - u_0}{u_\infty - \omega_{M_i}(t)}\right) = \tau_M^{-1} t

assuming :math:`u_\infty > u_0`. By then measuring :math:`\omega_{M_i}` and :math:`t` one can
estimate :math:`\tau_M` by using least squares regression. Note the data points for the regression
should be selected such that the problem is well conditioned i.e.,
:math:`\omega_{M_i} \lesssim u_\infty`.

In :numref:`tau_motor_dynamics` the time constant is estimated. One can see that it does vary
and decrease with an increasing :math:`u_0`, introducing a non-linearity. Moreover,
:math:`\tau_M` varies for positive and negative steps.

The seen effects have to be neglected to keep linearity. Therefore, the resulting time constant
is given by the mean of the steps responses where :math:`\omega_M \in [400, 800]` i.e., within
normal operating conditions. This gives :math:`\tau_M = 0.08`.

.. _tau_motor_dynamics:


    Positive and negative motor step responses (with mounted propeller). The time constant
    is estimated for each step using MLSE.

On a further note. The approximation of using a first order low pass filter is fine. But from the
figure it becomes clear that better approximations of higher order exist. An improvement would
be to empirical derive such a system - by using system identification.

Linearized State Space
-----------------------
The same linearized (SIMO) state-space representation as derived in
`Design-Modeling-and-Control-of-an-Octocopter`_ (Section 3.7) is used i.e.,

.. math::

    \mathbf{\dot{x}_i} &= \mathbf{A_i x_i} + \mathbf{B_i} u_i \\
    \mathbf{y_i} &= \mathbf{C_i x_i} + \mathbf{D_i} u_i, i = 1,2,...,6

where :math:`\mathbf{x_i}\in\mathbb{R}^3`, :math:`\mathbf{y_i}\in\mathbb{R}^2` and

.. math::
    :label: state_space_matrices

    \mathbf{A_i}=
    \begin{bmatrix}
        0 & 1 & 0 \\
        0 & 0 & c_i \\
        0 & 0 & -\tfrac{1}{\tau_M}
    \end{bmatrix},
    \mathbf{B_i}=
    \begin{bmatrix}
        0 \\
        0 \\
        \tfrac{1}{\tau_M}
    \end{bmatrix},
    \mathbf{C_i}=
    \begin{bmatrix}
        1 & 0 & 0 \\
        0 & 1 & 0
    \end{bmatrix},
    \mathbf{D_i}= 0.

Here :math:`\mathbf{c} = [\tfrac{1}{m}, \tfrac{1}{m}, \tfrac{1}{m}, \tfrac{1}{I_{xx}},
\tfrac{1}{I_{yy}}, \tfrac{1}{I_{zz}}]`. For instance :math:`i = 4` corresponds to the
state-space representation in roll

.. math::

    \mathbf{x_4}=
    \begin{bmatrix}
        \phi \\
        \dot\phi \\
        M_{\phi}
    \end{bmatrix},
    u_4=u_\phi,
    c_4=\tfrac{1}{I_{xx}}.

Note that the final state e.g., :math:`M_{\phi} (= I_{xx}\ddot\phi)` is observed using a reduced observer,
see :ref:`force-torque-estimation`.

State Estimation
=================

Attitude Estimation
--------------------
For attitude control, the Euler angles :math:`\eta = [\phi, \theta, \psi]` and their respective
time derivatives (angular rates) :math:`\dot{\eta} = \omega` (in the linearized model) are
needed.

Here :math:`\omega` is simply given by the IMU's gyro, but :math:`\eta` has to be estimated. This
can be accomplished using all sensors (accelerometer, gyro and magnetometer) and is a common
problem. Without going into detail - geometrical relationships yield

.. math::

    \phi_{acc} &= \text{atan2}(-a_{By}, -a_{Bz}) \\
    \theta_{acc} &= \text{atan2}(a_{Bx}, \sqrt{a_{By}^2 + a_{Bz}^2}) \\
    \psi_{mag} &= \text{atan2}(-B_{Iy}, B_{Ix})

where

.. math::

    B_{Ix} &= B_{Bx}\cos(\theta) + B_{By}\sin(\phi)\sin(\theta) + B_{Bz}\sin(\theta)\cos(\phi) \\
    B_{Iy} &= B_{By}\cos(\phi) - B_{Bz}\sin(\phi)

and :math:`a_B` is the acceleration and :math:`B_B` is the earths magnetic field supplied by the
IMU in the body frame. Where :math:`B_{Ix}` and :math:`B_{Iy}` are the magnetic fields in the
inertial frame.

These estimates can be improved by using the gyro and a simple first order complementary
filter (see `IMU Data Fusing <http://www.olliw.eu/2013/imu-data-fusing/>`_)

.. math::

    \tilde{\phi}^{k} &= \text{cf}(\phi_{acc}^k, \dot{\phi}_{gyro}^k, \tilde{\phi}^{k-1}, \tau_{\phi}) \\
    \tilde{\theta}^{k} &= \text{cf}(\theta_{acc}^k, \dot{\theta}_{gyro}^k, \tilde{\theta}^{k-1}, \tau_{\theta}) \\
    \tilde{\psi}^{k} &= \text{cf}(\psi_{mag}^k, \dot{\psi}_{gyro}^k, \tilde{\psi}^{k-1}, \tau_{\psi})

where

.. math::

    y^{k} &= \text{cf}(u^k, \dot{u}^k, y^{k-1}, \tau) \\
            &= \alpha(y^{k-1} + \dot{u}^k\Delta t) + (1-\alpha)u^k

where :math:`\alpha = \tfrac{\tau}{\tau + \Delta t}` and :math:`\tau` is the cut-off frequency
(:math:`\tau = \tfrac{1}{2 \pi f_c}`). Note that the estimates also need range limiting
(module of angles) and offset compensation (gyro and hard iron).

In :numref:`attitude_estimation` the result of the attitude estimation is shown. Note the large
drift of the gyro.

.. _attitude_estimation:


    Attitude estimation of roll (:math:`\phi`), pitch (:math:`\theta`) and
    yaw (:math:`\psi`). Both unfiltered and complementary filter estimates.
    Here :math:`\tau_{\phi}=\tau_{\theta}=\tau_{\psi}` s.t. :math:`f_c=20` Hz.

Hard Iron Offset
^^^^^^^^^^^^^^^^^
Magnetic fields affecting the magnetometer other than earth's need to be compensated
for. One of those is hard iron (the other being soft iron) effects. These are static
magnetic fields e.g., components on the PCB.

These offsets can easily be estimated using least squares (offset of a sphere)

.. math::

    \underset{V}{\text{minimize}} (B-V)^T (B-V) = B^2.

To get a good estimate, the magnetometer should be rotated in space to excite all
directions, see :numref:`hard_iron_offset`.

.. _hard_iron_offset:


    Hard iron offset estimation and correction.

.. _force-torque-estimation:

Force and Torque Estimation
----------------------------
The final state of :eq:`state_space_matrices` (force/torque), here denoted
:math:`\tilde{x}_a` is not measured. It is instead estimated using a reduced
observer, see `Design-Modeling-and-Control-of-an-Octocopter`_ Section (4.2.3)
for details.

A first order backwards time-difference of the observer gives

.. math::

    \tilde{x}^k_a = \beta_1 (\tilde{x}^{k-1}_a -\alpha x^{k-1}_v) +
    \beta_2 x^{k}_v + \beta_3 u^k, \tilde{x}^0_a = 0

where

.. math::

    \beta_1 &= \frac{\tau_M}{\beta_4} \\
    \beta_2 &= -\frac{\alpha\Delta t (1+ \alpha \tau_M c_i)}{\beta_4} \\
    \beta_3 &= \frac{\Delta t}{\beta_4} \\
    \beta_4 &= \tau_M + \Delta t (1 + \alpha \tau_M c_i)

and :math:`x_v` is the (translational/rotational) velocity state of each
state-space, :math:`\alpha` a tuning parameter. Note that
:math:`\text{Re}(\alpha) > -\tfrac{1}{\tau_M c_i}` for stability.

Also note that when :math:`\alpha\rightarrow\infty` the observer will result
in a backwards time-difference of :math:`x_v` i.e., its derivative
(:math:`\dot{x}_v = x_a`).

Control
=================

State Control
-----------------
The drone's dynamics are stabilized using a full state feedback controller

.. math::
    :label: cont_state_feedback

    u = -\mathbf{Lx}.

Which allows for arbitrary pole placement, see `Design-Modeling-and-Control-of-an-Octocopter`_
for in depth details.

Discretized Feedback
^^^^^^^^^^^^^^^^^^^^
In :ref:`force-torque-estimation` the reduced observer is presented, including the control
input. Hence, by using :eq:`cont_state_feedback` and solving for :math:`u_k` one derives at the
final time-discretized feedback controller

.. math::
    :label: disc_state_feedback

    u^k = -\frac{l_1 x_1^k + (l_2 + l_3(\beta_2 + \alpha)) x_2^k + l_3\beta_1(u^{k-1}
    - \alpha x_2^{k-1})}{1 + l_3\beta_3}, u^0 = 0.

Pilot Control
^^^^^^^^^^^^^^^
Typically, the pilot controller (using the handheld controller), seeks for stability
of roll, pitch and yaw-rate.

To tune :math:`\mathbf{L}` and :math:`\alpha` (reduced observer), the step response of
the closed loop is analyzed, see :numref:`tune_ctrl_roll_pitch`-:numref:`tune_ctrl_yaw_rate`.

Note, an integrated state has been added for roll and pitch control (already in place
for yaw-rate) i.e., :math:`\mathbf{x}\in\mathbb{R}^4`.

.. _tune_ctrl_roll_pitch:


    Tuning and parameter selection for roll and pitch control.

.. _tune_ctrl_yaw_rate:


    Tuning and parameter selection for yaw-rate control.

In the above figures :math:`u` corresponds to :eq:`cont_state_feedback` and
:math:`\tilde{u}` to :eq:`disc_state_feedback`. The abs-max value of the integrated
state (reference error) is also shown to determine a suitable value for anti-windup
i.e., to handle a large overshoot/instability caused by the integration.

In :numref:`rc_gimbal_def_pilot` the RC-gimbal definitions for the pilot controller
are given.

.. _rc_gimbal_def_pilot:


    RC-gimbal definitions for the pilot controller. The arrow indicates
    positive direction. Note that thrust implies negative :math:`F_z` i.e., lift.

Motor Control
------------------
The body force and torque control inputs :math:`u_{Bz}`, :math:`u_{B\phi}`,
:math:`u_{B\theta}` and :math:`u_{B\psi}` have to be converted to individual
motor control inputs :math:`u_{M_i}`.

.. _motor_rotations:


    The drone motor rotational directions.

From :numref:`motor_rotations` one can derive the drone body forces and
torques generated by the motors

.. math::

    F_{Bx} &= 0 \\
    F_{By} &= 0 \\
    F_{Bz} &= - F_{M_1z} - F_{M_2} - F_{M_3} - F_{M_4z} \\
    M_{Bx} &= - l_xF_{M_1z} - l_xF_{M_2z} + l_xF_{M_3z} + l_xF_{M_4z} \\
    M_{By} &=   l_xF_{M_1z} - l_xF_{M_2z} - l_xF_{M_3z} + l_xF_{M_4z} \\
    M_{Bz} &= - M_{M_1z} + M_{M_2z} - M_{M_3z} + M_{M_4z}

where :math:`F_{M_ix} = F_{M_iy} = M_{M_ix} = M_{M_iy} = 0` and
:math:`l_x = 0.23` m (distance between body center of mass and motor).

In order to solve for the motor inputs one can use the fact that
:math:`F, M \propto \omega^2`, where :math:`\omega` is the angular rate of a
motor/propeller, see :numref:`ang_rate_sq_vs_thrust`.

.. _ang_rate_sq_vs_thrust:


    Motor angular rate and its corresponding generated thrust. Positive
    rotation corresponds to the "intended" propeller rotation i.e., not
    driven in reverse. Fitted a 1st-order polynomial :math:`y = X[p_1]^\intercal`.

Hence, the generated body forces and torques can be described as following

.. math::

    \begin{bmatrix}
        F_{Bz} \\
        M_{Bx} \\
        M_{By} \\
        M_{Bz}
    \end{bmatrix} =
    \underbrace{
        \begin{bmatrix}
            -c_{Fz} & -c_{Fz} & -c_{Fz} & -c_{Fz} \\
            -l_xc_{Fz} & -l_xc_{Fz} & l_xc_{Fz} & l_xc_{Fz} \\
            l_xc_{Fz} & -l_xc_{Fz} & -l_xc_{Fz} & l_xc_{Fz} \\
            -c_{Mz} & c_{Mz} & -c_{Mz} & c_{Mz}
        \end{bmatrix}
    }_H
    \begin{bmatrix}
        \omega_{M_1z}^2 \\
        \omega_{M_2z}^2 \\
        \omega_{M_3z}^2 \\
        \omega_{M_4z}^2
    \end{bmatrix}.

By computing :math:`H^{-1}` one gets

.. math::

    [\omega_{M_1z}^2, \omega_{M_2z}^2, \omega_{M_3z}^2, \omega_{M_4z}^2]^\intercal
    = H^{-1} [F_{Bz}, M_{Bx}, M_{By}, M_{Bz}]^\intercal

where

.. math::
    H^{-1} = \frac{1}{4}
        \begin{bmatrix}
            -\tfrac{1}{c_{Fz}} & -\tfrac{1}{l_xc_{Fz}} & \tfrac{1}{l_xc_{Fz}} & -\tfrac{1}{c_{Mz}} \\
            -\tfrac{1}{c_{Fz}} & -\tfrac{1}{l_xc_{Fz}} & -\tfrac{1}{l_xc_{Fz}} & \tfrac{1}{c_{Mz}} \\
            -\tfrac{1}{c_{Fz}} & \tfrac{1}{l_xc_{Fz}} & -\tfrac{1}{l_xc_{Fz}} & -\tfrac{1}{c_{Mz}} \\
            -\tfrac{1}{c_{Fz}} & \tfrac{1}{l_xc_{Fz}} & \tfrac{1}{l_xc_{Fz}} & \tfrac{1}{c_{Mz}}
        \end{bmatrix}.

From :numref:`ang_rate_sq_vs_thrust` it can be seen that :math:`c_{Fz}` is smaller (about half)
when the motor is reversing (negative rotation). This is probably due to the non-symmetrical
shape of the propeller. Hence, a non-linearity arises and :math:`H^{-1}` can't solely be used.
Therefore reversing will for now not be used, maybe in the future.

Anyhow, :numref:`ang_rate_sq_vs_thrust` also gives :math:`c_{Fz} = -8.37\times 10^{-6}` (positive rotation
from now on only). The torque constant is given by :math:`c_{Mz} = \tfrac{1}{50} c_{Fz}` - empirical
relation from the master thesis.

In :numref:`ang_rate_vs_command` the empirical relation between the raw motor
control inputs and the angular rates is given.

.. _ang_rate_vs_command:


    The motor angular rates and raw control inputs. Fitted a 1nd-order polynomial
    :math:`y = X[p_1, p_0]^\intercal`. Note, first 5 values are not included in the
    regression for a better fit - not a commonly used interval. Also note the
    symmetry about :math:`u`.

Hence, the final conversion is given by

.. math::
    u_{M_i} =
    \begin{cases}
        57\omega_{M_iz} - 9675 & \text{if } \omega_{M_iz} \geq 200 \\
        0 & \text{otherwise}
    \end{cases}.

Note, :math:`u_{M_i}` should also be range limited since is it a ``int16`` and reversing
is not used.

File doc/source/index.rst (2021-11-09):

.. Ugglan documentation master file, created by
   sphinx-quickstart on Sat Oct 12 09:47:25 2019.
   You can adapt this file completely to your liking, but it should at least
   contain the root `toctree` directive.

Welcome to Ugglan's documentation!
==================================
The drone a.k.a "Ugglan" (Swedish for owl) is a DIY build quadcopter,
using the Raspberry Pi Zero 2 W.

.. toctree::
   :maxdepth: 2
   :caption: Content

   development
   software_design
   hardware_design
   modeling_control

Indices and tables
==================

* :ref:`genindex`
* :ref:`search`

.. literalinclude:: ./figures/ugglan.txt

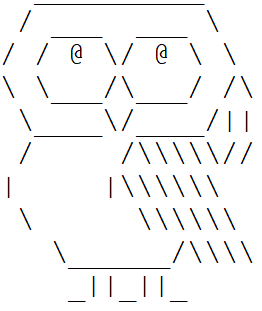
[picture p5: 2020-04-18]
doc/source/figures/ugglan.png

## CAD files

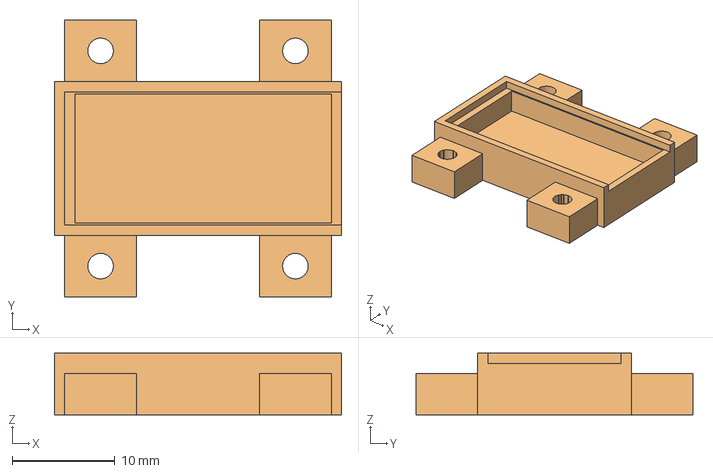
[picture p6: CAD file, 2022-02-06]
cad/imu_moutning_case.FCStd
28.0 x 27.0 x 6.00 mm
Body (Meshed)

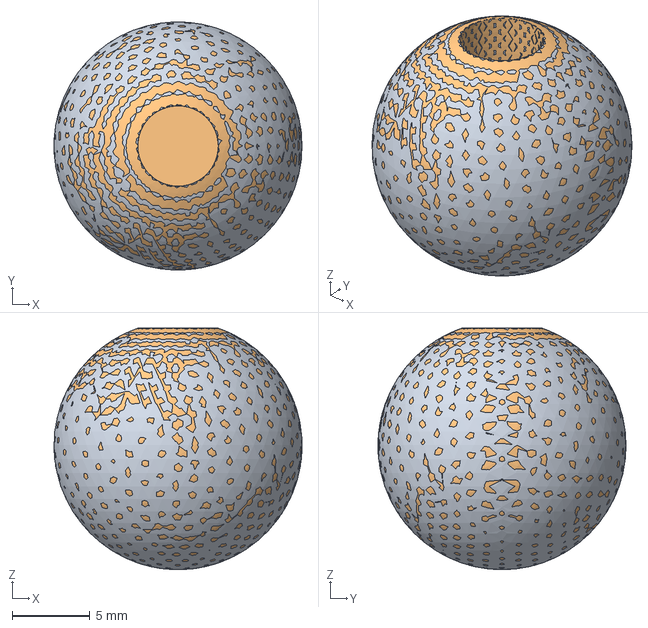
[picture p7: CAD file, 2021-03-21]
cad/landing_gear_foot.FCStd
16.0 x 16.0 x 15.6 mm
LandingGear
landing_gear_foot

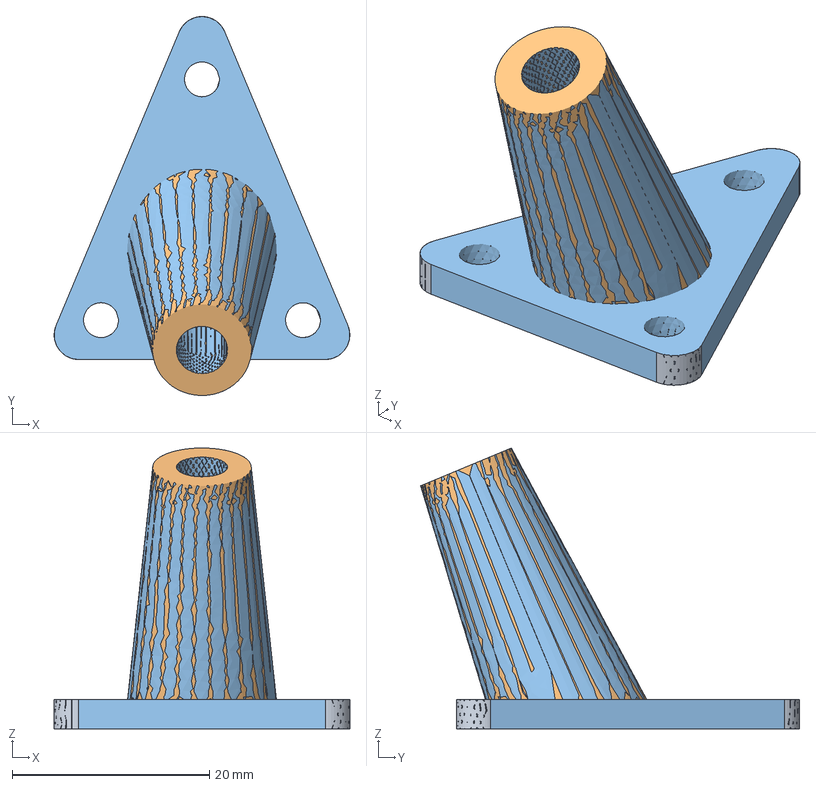
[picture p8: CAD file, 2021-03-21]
cad/landing_gear_base.FCStd
30.0 x 38.5 x 28.5 mm
Plate
landing_gear_base

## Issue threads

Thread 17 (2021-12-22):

Low-pass filter acceleration & update Kalman noise covariance matrix

real-tintin, 2021-12-22:
Due to vibration's the IMU acceleration needs to be low-pass filtered before entering the Kalman sensor fusion in the attitude estimation. Also, the R matrix should be computed such that the estimation can cope with linear acceleration e.g., dynamic R which favors the gyro more during acceleration (the acceleration should be used for long-term estimation due to bias in gyro).

real-tintin, 2021-12-22:
Inspiration https://ieeexplore.ieee.org/stamp/stamp.jsp?arnumber=9032181

real-tintin, 2021-12-22:
Consider using the gyro variance only, with some step function?

real-tintin, 2021-12-22:
To handle motor-induced vibration's we should also balance the motors + propellers.

real-tintin, 2022-01-07:
https://en.wikipedia.org/wiki/Bilinear_transform#Transformation_of_a_second-order_biquad

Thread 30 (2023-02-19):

Cast low accurate double data log signals to float

real-tintin, 2023-02-19:
Such as:

- RC receiver
- Esc voltage, temperature etc.

real-tintin, 2023-02-19:
How much relative storage would this safe?

real-tintin, 2023-04-23:
Would safe 20/69 (28 %) of all double signals i.e., 20 * 4 = 80 bytes.

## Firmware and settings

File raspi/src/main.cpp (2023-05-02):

#include <filesystem>
#include <string>
#include <thread>
#include <vector>

#include <afro_esc.hpp>
#include <attitude_estimation.hpp>
#include <config.hpp>
#include <data_log_queue.hpp>
#include <data_logger.hpp>
#include <drone_props.hpp>
#include <graceful_killer.hpp>
#include <i2c_conn.hpp>
#include <l3gd20h.hpp>
#include <lps25h.hpp>
#include <lsm303d.hpp>
#include <motor_control.hpp>
#include <pilot_control.hpp>
#include <serial_conn.hpp>
#include <streamer_server.hpp>
#include <task.hpp>
#include <tgyia6c.hpp>
#include <zmq_conn.hpp>

static const uint32_t TASK_ACC_MAG_EXEC_PERIOD_MS = 10;         // 100 Hz.
static const uint32_t TASK_GYRO_EXEC_PERIOD_MS = 10;            // 100 Hz.
static const uint32_t TASK_BAROMETER_EXEC_PERIOD_MS = 100;      // 10 Hz.
static const uint32_t TASK_STATE_EST_EXEC_PERIOD_MS = 10;       // 100 Hz.
static const uint32_t TASK_STATE_CTRL_EXEC_PERIOD_MS = 10;      // 100 Hz.
static const uint32_t TASK_ESC_READ_EXEC_PERIOD_MS = 1000;      // 1 Hz.
static const uint32_t TASK_ESC_WRITE_EXEC_PERIOD_MS = 10;       // 100 Hz.
static const uint32_t TASK_RC_RECEIVER_EXEC_PERIOD_MS = 10;     // 100 Hz.
static const uint32_t TASK_DATA_LOGGER_EXEC_PERIOD_MS = 100;    // 10 Hz.
static const uint32_t TASK_STREAMER_SERVER_EXEC_PERIOD_MS = 10; // 100 Hz.

static const uint8_t I2C_ADDRESS_ACC_MAG = LSM303D_I2C_ADDRESS;
static const uint8_t I2C_ADDRESS_GYRO = L3GD20H_I2C_ADDRESS;
static const uint8_t I2C_ADDRESS_BAROMETER = LPS25H_I2C_ADDRESS;

static const uint8_t I2C_ADDRESS_ESC_0 = 0x2a;
static const uint8_t I2C_ADDRESS_ESC_1 = 0x2b;
static const uint8_t I2C_ADDRESS_ESC_2 = 0x2c;
static const uint8_t I2C_ADDRESS_ESC_3 = 0x2d;

static const uint8_t N_ESC = droneprops::N_MOTORS;

static const uint32_t MAIN_SLEEP_MS = 1000;

static const double ATT_EST_INPUT_SAMPLE_RATE_S = 0.01; // 100 Hz (assumes IMU acc & gyro at 100 Hz)
static const double PILOT_CTRL_INPUT_SAMPLE_RATE_S = ATT_EST_INPUT_SAMPLE_RATE_S;

enum class TaskId
{
    AccMag,
    Gyro,
    Barometer,
    EscRead0,
    EscRead1,
    EscRead2,
    EscRead3,
    EscWrite0,
    EscWrite1,
    EscWrite2,
    EscWrite3,
    RcReceiver,
    StateEst,
    StateCtrl,
    DataLogger,
    StreamerServer
};

class TaskAccMag final : public Task
{
public:
    TaskAccMag(uint32_t exec_period_ms,
               std::string name,
               std::string i2c_device,
               uint8_t i2c_address,
               DataLogQueue &data_log_queue)
        : Task(exec_period_ms, name), _i2c_conn(i2c_device, i2c_address), _acc_mag(_i2c_conn),
          _data_log_queue(data_log_queue)
    {
    }

    ~TaskAccMag() = default;

protected:
    void _execute() override
    {
        _acc_mag.update();

        _data_log_queue.push(_acc_mag.get_acceleration_x(), DataLogSignal::ImuAccelerationX);
        _data_log_queue.push(_acc_mag.get_acceleration_y(), DataLogSignal::ImuAccelerationY);
        _data_log_queue.push(_acc_mag.get_acceleration_z(), DataLogSignal::ImuAccelerationZ);

        _data_log_queue.push(_acc_mag.get_magnetic_field_x(), DataLogSignal::ImuMagneticFieldX);
        _data_log_queue.push(_acc_mag.get_magnetic_field_y(), DataLogSignal::ImuMagneticFieldY);
        _data_log_queue.push(_acc_mag.get_magnetic_field_z(), DataLogSignal::ImuMagneticFieldZ);

        _data_log_queue.push(_acc_mag.get_status(), DataLogSignal::ImuAccMagStatus);
        _data_log_queue.push(uint8_t(TaskId::AccMag), DataLogSignal::TaskExecute);
    }

private:
    I2cConn _i2c_conn;
    Lsm303d _acc_mag;
    DataLogQueue &_data_log_queue;
};

class TaskGyro final : public Task
{
public:
    TaskGyro(uint32_t exec_period_ms,
             std::string name,
             std::string i2c_device,
             uint8_t i2c_address,
             DataLogQueue &data_log_queue)
        : Task(exec_period_ms, name), _i2c_conn(i2c_device, i2c_address), _gyro(_i2c_conn),
          _data_log_queue(data_log_queue)
    {
    }

    ~TaskGyro() = default;

protected:
    void _execute() override
    {
        _gyro.update();

        _data_log_queue.push(_gyro.get_angular_rate_x(), DataLogSignal::ImuAngularRateX);
        _data_log_queue.push(_gyro.get_angular_rate_y(), DataLogSignal::ImuAngularRateY);
        _data_log_queue.push(_gyro.get_angular_rate_z(), DataLogSignal::ImuAngularRateZ);

        _data_log_queue.push(_gyro.get_status(), DataLogSignal::ImuGyroStatus);
        _data_log_queue.push(uint8_t(TaskId::Gyro), DataLogSignal::TaskExecute);
    }

private:
    I2cConn _i2c_conn;
    L3gd20h _gyro;
    DataLogQueue &_data_log_queue;
};

class TaskBarometer final : public Task
{
public:
    TaskBarometer(uint32_t exec_period_ms,
                  std::string name,
                  std::string i2c_device,
                  uint8_t i2c_address,
                  DataLogQueue &data_log_queue)
        : Task(exec_period_ms, name), _i2c_conn(i2c_device, i2c_address), _barometer(_i2c_conn),
          _data_log_queue(data_log_queue)
    {
    }

    ~TaskBarometer() = default;

protected:
    void _execute() override
    {
        _barometer.update();

        _data_log_queue.push(_barometer.get_pressure(), DataLogSignal::ImuPressure);
        _data_log_queue.push(_barometer.get_temperature(), DataLogSignal::ImuTemperature);

        _data_log_queue.push(_barometer.get_status(), DataLogSignal::ImuBarometerStatus);
        _data_log_queue.push(uint8_t(TaskId::Barometer), DataLogSignal::TaskExecute);
    }

private:
    I2cConn _i2c_conn;
    Lps25h _barometer;
    DataLogQueue &_data_log_queue;
};

class TaskStateEst final : public Task
{
public:
    TaskStateEst(uint32_t exec_period_ms,
                 std::string name,
                 double input_sample_rate_s,
                 att_est::Config config,
                 DataLogQueue &data_log_queue)
        : Task(exec_period_ms, name), _estimator(input_sample_rate_s, config), _data_log_queue(data_log_queue)
    {
    }

    ~TaskStateEst() = default;

protected:
    void _execute() override
    {
        _data_log_queue.last_signal_data(&_imu_uncompensated.acc_x, DataLogSignal::ImuAccelerationX);
        _data_log_queue.last_signal_data(&_imu_uncompensated.acc_y, DataLogSignal::ImuAccelerationY);
        _data_log_queue.last_signal_data(&_imu_uncompensated.acc_z, DataLogSignal::ImuAccelerationZ);

        _data_log_queue.last_signal_data(&_imu_uncompensated.ang_rate_x, DataLogSignal::ImuAngularRateX);
        _data_log_queue.last_signal_data(&_imu_uncompensated.ang_rate_y, DataLogSignal::ImuAngularRateY);
        _data_log_queue.last_signal_data(&_imu_uncompensated.ang_rate_z, DataLogSignal::ImuAngularRateZ);

        _data_log_queue.last_signal_data(&_imu_uncompensated.mag_field_x, DataLogSignal::ImuMagneticFieldX);
        _data_log_queue.last_signal_data(&_imu_uncompensated.mag_field_y, DataLogSignal::ImuMagneticFieldY);
        _data_log_queue.last_signal_data(&_imu_uncompensated.mag_field_z, DataLogSignal::ImuMagneticFieldZ);

        _estimator.update(_imu_uncompensated);

        _attitude = _estimator.get_attitude();
        _imu_compensated = _estimator.get_imu_compensated();

        _data_log_queue.push(_attitude.roll.angle, DataLogSignal::StateEstRoll);
        _data_log_queue.push(_attitude.pitch.angle, DataLogSignal::StateEstPitch);
        _data_log_queue.push(_attitude.yaw.angle, DataLogSignal::StateEstYaw);

        _data_log_queue.push(_attitude.roll.rate, DataLogSignal::StateEstRollRate);
        _data_log_queue.push(_attitude.pitch.rate, DataLogSignal::StateEstPitchRate);
        _data_log_queue.push(_attitude.yaw.rate, DataLogSignal::StateEstYawRate);

        _data_log_queue.push(_attitude.roll.acc, DataLogSignal::StateEstRollAcc);
        _data_log_queue.push(_attitude.pitch.acc, DataLogSignal::StateEstPitchAcc);
        _data_log_queue.push(_attitude.yaw.acc, DataLogSignal::StateEstYawAcc);

        _data_log_queue.push(_imu_compensated.acc_x, DataLogSignal::StateEstCompAccX);
        _data_log_queue.push(_imu_compensated.acc_y, DataLogSignal::StateEstCompAccY);
        _data_log_queue.push(_imu_compensated.acc_z, DataLogSignal::StateEstCompAccZ);

        _data_log_queue.push(_imu_compensated.ang_rate_x, DataLogSignal::StateEstCompAngRateX);
        _data_log_queue.push(_imu_compensated.ang_rate_y, DataLogSignal::StateEstCompAngRateY);
        _data_log_queue.push(_imu_compensated.ang_rate_z, DataLogSignal::StateEstCompAngRateZ);

        _data_log_queue.push(_imu_compensated.mag_field_x, DataLogSignal::StateEstCompMagFieldX);
        _data_log_queue.push(_imu_compensated.mag_field_y, DataLogSignal::StateEstCompMagFieldY);
        _data_log_queue.push(_imu_compensated.mag_field_z, DataLogSignal::StateEstCompMagFieldZ);

        _data_log_queue.push(_estimator.is_calibrated(), DataLogSignal::StateEstAttIsCalibrated);
        _data_log_queue.push(_estimator.is_standstill(), DataLogSignal::StateEstAttIsStandstill);

        _data_log_queue.push(uint8_t(TaskId::StateEst), DataLogSignal::TaskExecute);
    }

private:
    att_est::Imu _imu_uncompensated;
    att_est::Imu _imu_compensated;
    att_est::Attitude _attitude;
    att_est::Estimator _estimator;

    DataLogQueue &_data_log_queue;
};

class TaskStateCtrl final : public Task
{
public:
    TaskStateCtrl(uint32_t exec_period_ms,
                  std::string name,
                  double input_sample_rate_s,
                  PilotCtrlConfig config,
                  DataLogQueue &data_log_queue)
        : Task(exec_period_ms, name), _pilot_ctrl(input_sample_rate_s, config), _data_log_queue(data_log_queue)
    {
    }

    ~TaskStateCtrl() = default;

protected:
    void _execute() override
    {
        _exec_pilot_ctrl();
        _exec_motor_ctrl();

        _data_log_queue.push(uint8_t(TaskId::StateCtrl), DataLogSignal::TaskExecute);
    }

private:
    bool _att_est_is_calibrated;
    bool _state_ctrl_reset;
    att_est::Attitude _attitude;

    double _gimbal_left_x, _gimbal_left_y, _gimbal_right_x, _gimbal_right_y;

    PilotControl _pilot_ctrl;
    PilotCtrlRef _ctrl_ref;

    DataLogQueue &_data_log_queue;

    BodyControl _body_ctrl;
    MotorControl _motor_ctrl;

    static constexpr DataLogSignal _sid_motor_cmd[N_ESC] = {DataLogSignal::EscMotorCmd0,
                                                            DataLogSignal::EscMotorCmd1,
                                                            DataLogSignal::EscMotorCmd2,
                                                            DataLogSignal::EscMotorCmd3};

    void _exec_pilot_ctrl()
    {
        _data_log_queue.last_signal_data(&_att_est_is_calibrated, DataLogSignal::StateEstAttIsCalibrated, false);
        _data_log_queue.last_signal_data(&_state_ctrl_reset, DataLogSignal::StateCtrlReset, true);

        if (_state_ctrl_reset)
        {
            _pilot_ctrl.reset();
        }
        else if (_att_est_is_calibrated && !_state_ctrl_reset)
        {
            _data_log_queue.last_signal_data(&_attitude.roll.angle, DataLogSignal::StateEstRoll);
            _data_log_queue.last_signal_data(&_attitude.pitch.angle, DataLogSignal::StateEstPitch);
            _data_log_queue.last_signal_data(&_attitude.yaw.angle, DataLogSignal::StateEstYaw);

            _data_log_queue.last_signal_data(&_attitude.roll.rate, DataLogSignal::StateEstRollRate);
            _data_log_queue.last_signal_data(&_attitude.pitch.rate, DataLogSignal::StateEstPitchRate);
            _data_log_queue.last_signal_data(&_attitude.yaw.rate, DataLogSignal::StateEstYawRate);

            _data_log_queue.last_signal_data(&_attitude.roll.acc, DataLogSignal::StateEstRollAcc);
            _data_log_queue.last_signal_data(&_attitude.pitch.acc, DataLogSignal::StateEstPitchAcc);
            _data_log_queue.last_signal_data(&_attitude.yaw.acc, DataLogSignal::StateEstYawAcc);

            _data_log_queue.last_signal_data(&_gimbal_left_x, DataLogSignal::RcGimbalLeftX);
            _data_log_queue.last_signal_data(&_gimbal_left_y, DataLogSignal::RcGimbalLeftY);
            _data_log_queue.last_signal_data(&_gimbal_right_x, DataLogSignal::RcGimbalRightX);
            _data_log_queue.last_signal_data(&_gimbal_right_y, DataLogSignal::RcGimbalRightY);

            _ctrl_ref = tgyia6c_to_pilot_ctrl_ref(_gimbal_left_x, _gimbal_left_y, _gimbal_right_x, _gimbal_right_y);

            _pilot_ctrl.update(_attitude, _ctrl_ref);
        }

        _body_ctrl = _pilot_ctrl.get_ctrl();

        _data_log_queue.push(_ctrl_ref.roll, DataLogSignal::StateCtrlRollRef);
        _data_log_queue.push(_ctrl_ref.pitch, DataLogSignal::StateCtrlPitchRef);
        _data_log_queue.push(_ctrl_ref.yaw_rate, DataLogSignal::StateCtrlYawRateRef);
        _data_log_queue.push(_ctrl_ref.f_z, DataLogSignal::StateCtrlFzRef);

        _data_log_queue.push(_pilot_ctrl.get_state(PilotCtrlState::Phi0), DataLogSignal::StateCtrlPhi0);
        _data_log_queue.push(_pilot_ctrl.get_state(PilotCtrlState::Phi1), DataLogSignal::StateCtrlPhi1);
        _data_log_queue.push(_pilot_ctrl.get_state(PilotCtrlState::Phi2), DataLogSignal::StateCtrlPhi2);
        _data_log_queue.push(_pilot_ctrl.get_state(PilotCtrlState::Phi3), DataLogSignal::StateCtrlPhi3);

        _data_log_queue.push(_pilot_ctrl.get_state(PilotCtrlState::Theta0), DataLogSignal::StateCtrlTheta0);
        _data_log_queue.push(_pilot_ctrl.get_state(PilotCtrlState::Theta1), DataLogSignal::StateCtrlTheta1);
        _data_log_queue.push(_pilot_ctrl.get_state(PilotCtrlState::Theta2), DataLogSignal::StateCtrlTheta2);
        _data_log_queue.push(_pilot_ctrl.get_state(PilotCtrlState::Theta3), DataLogSignal::StateCtrlTheta3);

        _data_log_queue.push(_pilot_ctrl.get_state(PilotCtrlState::Psi0), DataLogSignal::StateCtrlPsi0);
        _data_log_queue.push(_pilot_ctrl.get_state(PilotCtrlState::Psi1), DataLogSignal::StateCtrlPsi1);
        _data_log_queue.push(_pilot_ctrl.get_state(PilotCtrlState::Psi2), DataLogSignal::StateCtrlPsi2);

        _data_log_queue.push(_body_ctrl.m_x, DataLogSignal::StateCtrlMx);
        _data_log_queue.push(_body_ctrl.m_y, DataLogSignal::StateCtrlMy);
        _data_log_queue.push(_body_ctrl.m_z, DataLogSignal::StateCtrlMz);
        _data_log_queue.push(_body_ctrl.f_z, DataLogSignal::StateCtrlFz);
    }

    void _exec_motor_ctrl()
    {
        _motor_ctrl = body_to_motor_controls(_body_ctrl);

        for (uint8_t i_esc = 0; i_esc < N_ESC; i_esc++)
        {
            _data_log_queue.push(_motor_ctrl[i_esc], _sid_motor_cmd[i_esc]);
        }
    }
};

class TaskEscRead final : public Task
{
public:
    TaskEscRead(uint32_t exec_period_ms, std::string name, AfroEsc (&esc)[N_ESC], DataLogQueue &data_log_queue)
        : Task(exec_period_ms / N_ESC, name), _esc(esc), _data_log_queue(data_log_queue)
    {
    }

    ~TaskEscRead() = default;

protected:
    void _execute() override
    {
        uint8_t i_esc = _load_balance_step;
        _esc[i_esc].read();

        _data_log_queue.push(_esc[i_esc].get_is_alive(), _sid_is_alive[i_esc]);
        _data_log_queue.push(_esc[i_esc].get_angular_rate(), _sid_ang_rate[i_esc]);
        _data_log_queue.push(_esc[i_esc].get_voltage(), _sid_voltage[i_esc]);
        _data_log_queue.push(_esc[i_esc].get_current(), _sid_current[i_esc]);
        _data_log_queue.push(_esc[i_esc].get_temperature(), _sid_temperature[i_esc]);
        _data_log_queue.push(_esc[i_esc].get_status(), _sid_status[i_esc]);
        _data_log_queue.push(uint8_t(_task_read_ids[i_esc]), DataLogSignal::TaskExecute);

        _load_balance_step = (_load_balance_step + 1) % N_ESC;
    }

private:
    AfroEsc (&_esc)[N_ESC];
    DataLogQueue &_data_log_queue;

    static constexpr DataLogSignal _sid_is_alive[N_ESC] = {
        DataLogSignal::EscIsAlive0, DataLogSignal::EscIsAlive1, DataLogSignal::EscIsAlive2, DataLogSignal::EscIsAlive3};

    static constexpr DataLogSignal _sid_ang_rate[N_ESC] = {DataLogSignal::EscAngularRate0,
                                                           DataLogSignal::EscAngularRate1,
                                                           DataLogSignal::EscAngularRate2,
                                                           DataLogSignal::EscAngularRate3};

    static constexpr DataLogSignal _sid_voltage[N_ESC] = {
        DataLogSignal::EscVoltage0, DataLogSignal::EscVoltage1, DataLogSignal::EscVoltage2, DataLogSignal::EscVoltage3};

    static constexpr DataLogSignal _sid_current[N_ESC] = {
        DataLogSignal::EscCurrent0, DataLogSignal::EscCurrent1, DataLogSignal::EscCurrent2, DataLogSignal::EscCurrent3};

    static constexpr DataLogSignal _sid_temperature[N_ESC] = {DataLogSignal::EscTemperature0,
                                                              DataLogSignal::EscTemperature1,
                                                              DataLogSignal::EscTemperature2,
                                                              DataLogSignal::EscTemperature3};

    static constexpr DataLogSignal _sid_status[N_ESC] = {
        DataLogSignal::EscStatus0, DataLogSignal::EscStatus1, DataLogSignal::EscStatus2, DataLogSignal::EscStatus3};

    static constexpr TaskId _task_read_ids[N_ESC] = {
        TaskId::EscRead0, TaskId::EscRead1, TaskId::EscRead2, TaskId::EscRead3};

    uint8_t _load_balance_step = 0;
};

class TaskEscWrite final : public Task
{
public:
    TaskEscWrite(uint32_t exec_period_ms, std::string name, AfroEsc (&esc)[N_ESC], DataLogQueue &data_log_queue)
        : Task(exec_period_ms, name), _esc(esc), _data_log_queue(data_log_queue)
    {
    }

    ~TaskEscWrite() = default;

protected:
    void _setup() override
    {
        _arm_escs();
        _push_task_state_to_data_log(DataLogSignal::TaskSetup);
    }

    void _execute() override
    {
        EscState user_reqeusted_esc_state = _get_user_requested_esc_state();
        EscState limited_esc_state = _limit_change_of_esc_state(user_reqeusted_esc_state, _old_esc_state);

        _update_escs(limited_esc_state);
        _old_esc_state = limited_esc_state;

        _push_task_state_to_data_log(DataLogSignal::TaskExecute);
    }

    void _finish() override
    {
        _halt_escs();
        _push_task_state_to_data_log(DataLogSignal::TaskFinish);
    }
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
int main()
{
    config::Config config;
    config.load();

    logger.set_level(config.get_logger_level());
    config.print_to_debug();

    DataLogQueue data_log_queue;
    std::vector<std::unique_ptr<Task>> tasks;

    I2cConn esc_conn_0(config.get_i2c_device_esc(), I2C_ADDRESS_ESC_0);
    I2cConn esc_conn_1(config.get_i2c_device_esc(), I2C_ADDRESS_ESC_1);
    I2cConn esc_conn_2(config.get_i2c_device_esc(), I2C_ADDRESS_ESC_2);
    I2cConn esc_conn_3(config.get_i2c_device_esc(), I2C_ADDRESS_ESC_3);

    AfroEsc esc[N_ESC] = {esc_conn_0, esc_conn_1, esc_conn_2, esc_conn_3};

    tasks.emplace_back(new TaskAccMag(
        TASK_ACC_MAG_EXEC_PERIOD_MS, "ImuAccMag", config.get_i2c_device_imu(), I2C_ADDRESS_ACC_MAG, data_log_queue));

    tasks.emplace_back(new TaskGyro(
        TASK_GYRO_EXEC_PERIOD_MS, "ImuGyro", config.get_i2c_device_imu(), I2C_ADDRESS_GYRO, data_log_queue));

    tasks.emplace_back(new TaskBarometer(TASK_BAROMETER_EXEC_PERIOD_MS,
                                         "ImuBarometer",
                                         config.get_i2c_device_imu(),
                                         I2C_ADDRESS_BAROMETER,
                                         data_log_queue));

    tasks.emplace_back(new TaskEscWrite(TASK_ESC_WRITE_EXEC_PERIOD_MS, "EscWrite", esc, data_log_queue));

    tasks.emplace_back(new TaskEscRead(TASK_ESC_READ_EXEC_PERIOD_MS, "EscRead", esc, data_log_queue));

    tasks.emplace_back(
        new TaskRcReceiver(TASK_RC_RECEIVER_EXEC_PERIOD_MS, "RcReceiver", config.get_serial_device(), data_log_queue));

    tasks.emplace_back(new TaskStateEst(
        TASK_STATE_EST_EXEC_PERIOD_MS, "StateEst", ATT_EST_INPUT_SAMPLE_RATE_S, config.get_att_est(), data_log_queue));

    tasks.emplace_back(new TaskStateCtrl(TASK_STATE_CTRL_EXEC_PERIOD_MS,
                                         "StateCtrl",
                                         PILOT_CTRL_INPUT_SAMPLE_RATE_S,
                                         config.get_pilot_ctrl(),
                                         data_log_queue));

    tasks.emplace_back(
        new TaskDataLogger(TASK_DATA_LOGGER_EXEC_PERIOD_MS, "DataLogger", config.get_data_log_root(), data_log_queue));

    tasks.emplace_back(new TaskStreamerServer(TASK_STREAMER_SERVER_EXEC_PERIOD_MS,
                                              "StreamerServer",
                                              config.get_zmq_address_request(),
                                              config.get_zmq_address_stream(),
                                              data_log_queue));

    for (auto const &task : tasks)
    {
        task->launch();
    }
    wait_for_shutdown(data_log_queue);
    for (auto const &task : tasks)
    {
        task->teardown();
    }

    return 0;
}

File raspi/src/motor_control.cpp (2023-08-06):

#include <motor_control.hpp>

static const double INV_THRUST_CONST_FZ = 35211;   // 1 / (4 * c_fz) [rad/Ns]
static const double INV_THRUST_CONST_MZ = 153093;  // 1 / (4 * l_x * c_fz) [rad/Nms]
static const double INV_TORQUE_CONST_MZ = 1760563; // 1 / (4 * c_mz) [rad/Nms]

static const double RAW_MOTOR_POLY_0 = 45.0;
static const double RAW_MOTOR_POLY_1 = -6656.0;

static const double MIN_SQ_ANG_RATE = pow(200, 2); // [rad^2/s^2]

typedef std::array<double, droneprops::N_MOTORS> AngularRate;

static AngularRate _body_to_ang_rates(BodyControl &body);
static MotorControl _ang_rates_to_motor_controls(AngularRate &ang_rates);

MotorControl body_to_motor_controls(BodyControl &body_controls)
{
    AngularRate ang_rates = _body_to_ang_rates(body_controls);
    MotorControl motor_controls = _ang_rates_to_motor_controls(ang_rates);

    return motor_controls;
}

static AngularRate _body_to_ang_rates(BodyControl &body_controls)
{
    AngularRate ang_rates = {0.0, 0.0, 0.0, 0.0};
    AngularRate sq_ang_rates = {0.0, 0.0, 0.0, 0.0};

    double f_z = INV_THRUST_CONST_FZ * body_controls.f_z;
    double m_x = INV_THRUST_CONST_MZ * body_controls.m_x;
    double m_y = INV_THRUST_CONST_MZ * body_controls.m_y;
    double m_z = INV_TORQUE_CONST_MZ * body_controls.m_z;

    sq_ang_rates[0] = -f_z - m_x + m_y - m_z;
    sq_ang_rates[1] = -f_z - m_x - m_y + m_z;
    sq_ang_rates[2] = -f_z + m_x - m_y - m_z;
    sq_ang_rates[3] = -f_z + m_x + m_y + m_z;

    for (uint8_t motor_i = 0; motor_i < droneprops::N_MOTORS; motor_i++)
    {
        if (sq_ang_rates[motor_i] >= MIN_SQ_ANG_RATE)
        {
            ang_rates[motor_i] = sqrt(sq_ang_rates[motor_i]);
        }
    }

    return ang_rates;
}

static MotorControl _ang_rates_to_motor_controls(AngularRate &ang_rates)
{
    double motor_control = 0.0;
    MotorControl motor_controls = {0, 0, 0, 0};

    for (uint8_t motor_i = 0; motor_i < droneprops::N_MOTORS; motor_i++)
    {
        motor_control = RAW_MOTOR_POLY_0 * ang_rates[motor_i] + RAW_MOTOR_POLY_1;

        if (motor_control < 0.0)
        {
            motor_control = 0.0;
        }
        if (motor_control > INT16_MAX)
        {
            motor_control = INT16_MAX;
        }

        motor_controls[motor_i] = int16_t(motor_control);
    }

    return motor_controls;
}

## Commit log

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2020-04-13 Add doc for compling and flashing of the ESC.
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2020-04-19 Update thrust estimation analysis and doc, use linear Hinv and non-negative rotation.
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2020-05-01 Add base class for pololu alt imu. Update doc.
2020-05-01 Add test for l2gd20h aka gyro. Update pololu base class.
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2020-05-03 Add lib for lsm303d. Remove addrs for not used imu i2c registers.
2020-07-17 Begin implementing afro ESC class. Create helper class wall time.
2020-07-17 Return int32 instead of double from wall time. Add tests for afro esc. Use crocodile for all includes (added to path).
2020-07-17 Handle some valid and some invalid regs in pololu alt imu. Refactor afro esc methods.
2020-07-21 Write u-test for afro esc get methods. Refactor conversion logic.
2020-07-24 Make afro esc is alive get method public. Rpm is now double.
2020-07-24 Create task class and u-test. Add compiler support for threading. Change class instantiation method to avoid calling the copy constructor.
    [test_pololu_alt_imu.cpp]
2020-08-18 Test data log queue with multiple threads calling.
2020-09-15 Cross compile ugglan for target (Raspberry Pi), use GCC 9.1 (for consistency to unit test). Fix various issues in i2c and serial conn wrappers.
    [i2c_conn.cpp, main.cpp]
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2020-09-27 Add i2c address arg to i2c stub to mimic the real deal.
2020-09-27 Glue the application together. Use same interface in serial conn stub as the real deal.
2020-09-28 Add more logs. Cast rc receiver enums when data logging. Move up in main: set of logger level and print of envs. Should be run before all task constructors.
2020-09-28 Fix bug in serial conn read when no bytes available.
    [afro_esc.cpp]
2020-09-29 Update doc with setup on Raspbian. Fix bug in i2c conn. Update main (for debug) and service.
    [i2c_conn.cpp, main.cpp]
2020-09-29 Remove task exec exceeded cb, not used atm (revert if needed). Don't use nullptr for cb!
    [main.cpp]
2020-10-02 Add support for type bool in data logging. Update naming of ESC angular rate (from rpm, which is its unit). Fix RC sample rate in doc. Fix bugs in task esc: execution period and reading. Update exec 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
    [afro_esc.cpp, i2c_conn.cpp, main.cpp]
2020-10-03 Load balance task esc read. Use high res clock to improve timing. Update various logger levels.
2020-10-04 Make use of SW implmented i2c device (gpio overlays) for ESC. This to enable fast mode for IMU and increase performance.
2020-10-07 Breakout esc read into its own task. Update AfroEsc class: read/write thread safe, refactor arming and timing for ang-rate computation.
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2020-10-13 Add wiring diagram to doc. Explicitly state that pythons venv is used (not virtualenv).
2020-10-14 Update README and correct an error in the wiring diagram.
2020-10-14 Update doc section regarding modeling and nomenclature for reference frame.
2020-10-17 Be explicit about python version. Add missing resistor to wiring diagram.
2020-10-25 Fix bug in complementary filter for attitude est and update doc. Write inertia section on doc.
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2020-11-08 Analyze and add hard iron offset compensation. Align yaw direction with axis def.
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2020-12-03 Add least sqaures paragraph to motor dynamics section.
2020-12-06 Add motor time constant estimatio.. Update doc correspondingly. Data log reader option: re-sample to fixed rate. Use in attitude and hard iron offset estimation.
2020-12-12 Move motor ctrl to attitude estimation and control task. Add the conversion of motor angular rates to commands. Minor changes to the scripts for the estimation of the motor dynamics. Return motor ang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
2021-01-03 Refactor analysis of motor time constant. Add the emperical motor time constant estimation to doc. Plot motor command in general data analysis.
2021-01-03 Improve the motor time constant estimation by only using continues values and adding a lower limit for the mlse.
2021-01-08 Created tools for analysis and tuning of state control laws. Updated doc: Nomenclature (force and torque), linearized state space, reduced observer and state feedback control.
2021-01-17 Implement pilot based controller in target C++. Analyze state ctrl signals offline. Adjust attitude est comp filter settings - lower cut-off freq. Make sure esc's halt during shutdown.
2021-01-21 Tune intg-ctrl to be more responsive against modelling errors. Re-work operator state machine and logic. Set motor ctrl angular-rate to zero if below linear region. Fix minor things. Update doc.
    [afro_esc.cpp, main.cpp, motor_control.cpp]
2021-01-24 Update pilot ctrl ref definition and doc. Increase anti-wind up to 75 % of ref. Update IMU sample rate's to align with 50 Hz est/ctrl loop.
2021-03-14 Larger update of the multi body tool: * Add new sphere body type * Possibility to perform rotation in body frame * Refactoring and unit testing of new features
    Add new drone landing gear to its multi body and update figures in doc.
2021-03-18 Adding CAD models of the landing gear and updating the doc with the bifilar pendulum experiment for the estimation of the moment of inertia about z.
    [landing_gear_base.FCStd, landing_gear_foot.FCStd]
2021-03-21 Env vars as config, refactoring and update cad model.
    * Move systemd envs to file.
    * Read some pilot ctrl tuning parameters from env variables for easier config.
    * Refactor logger.
    * Use constexpr where in data logger template if case for an explicit optimze.
    * Decrease hole size on foot cad model (for friction fit).
    [landing_gear_base.FCStd, landing_gear_foot.FCStd]
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2021-09-15 A lot of stuff: * Added Kalman filter to attitude est. * Fixed issues in the matrix class. * Added new env variables for tuning the Kalman filter. * Uncomment of the pilot ctrl lib. This is a TODO.
    [main.cpp]
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2021-09-15 Only share x-axis in data log subplots (as sharing between figures is bugy).
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2021-09-21 Use rolling variance for Kalman R attitude estimation. Only exec ctrl when the attitude estimation is calibrated.
2021-09-30 Update esc write logic given the requested user input and reset pilot ctrl if not runing.
    [afro_esc.cpp, main.cpp]
2021-11-09 Update build process, env etc. after upgrade to pi zero 2 w.
    * Upgrade to raspi docker image to debian bullseye (and now share
    between test and dpkg build).
    * Breakout interface dev paths and update the serial gpio path.
    * Update doc alongside. Add short analysis of performance between the
    single and multi core pi zero.
    [main.cpp]
2021-11-10 Update the task exec rates, now that the cpu is upgraded.
    * Increase exec rate of IMU (acc+gyro+mag), state est, state ctrl
    and esc write to 100 Hz.
    * Lower exec rate of IMU pressure to 10 Hz (not really used atm).
    * Lower exec rate of ESC write to 10 Hz (not really used atm).
2021-12-02 Implement a non-linear 6-dof drone simulator with an GUI. Also:
    * Replaced Matplotlib with PyQtGraph to generate the 3d drone multi-body model.
    * Added Simulator section in the doc and updated multi-body figures.
    * Refactored the data-log attitude estimation tool.
    * Disable docker caching action as it seems to be full (fix in later).
    * Rm unused include in att estimation header.
    * Split the raspi docker image between host and target (arm v7)
2021-12-07 Use qemu gh action and compile raspi for target (arm v7) in ci.
2021-12-10 Add option to 6dof sim to init motors as fz and refactor menu/config.
2021-12-22 Implement gui tool for iir filter design.
    The tool let's you load and analyze a data log file and signal for
    filter design e.g., order, type or cut-off frequencies.
2022-01-05 Add script to analyze the motor and propeller induced vibrations.
    Also:
    * Add section to doc of the motor and propeller vibration analysis and balancing.
    * Update motor_dyn script help and comment.
2022-01-17 Add psd subplot to motor vibration analysis and update doc.
2022-02-06 Add cad model for the imu mounting case.
    [imu_moutning_case.FCStd]
2022-03-12 Improve local build speed of C++ app.
    * By generating dependencies.
    * Mounting into container.
2022-11-09 Add close methods to i2c and serial conn. Easier to test in the future and symmetry.
2023-01-03 Support mac (#25)
    Add support for my MacBook M2 (arm).
    Also refactor 6dof simulator and add reset logic.
2023-02-04 Implement a wireless streaming service on ugglan.
    The c++ server is fully implemented and a basic python client
    exists. Also made a lot of refactoring. A selection of it follows.
    - Add header guards to gzip lib and throw error if empty input
    - Rename c++ utils to common_utils to avoid name clashing
    - Refactor data log e.g., move logic to data_log_utils
    - Make use of size_t where applicable
    - Throw c++ style runtime error in base64 lib, rm new line by default
    [config.cpp, i2c_conn.cpp, main.cpp]
2023-02-04 Refactor raspi build chain and turn all warnings into errors and fix them.
2023-02-25 Estimate accelerometer static errors and compensate. Refactor target c++ attitude estimation.
    - Update doc.
    - Rename offset -> bias w.r.t IMU error compensation.
    - Add namespace string for closing namespaces.
    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
    [config.cpp, main.cpp]
2023-02-25 Align offline data log attitude estimation analysis tool with target implementation.
    Also, fix name of env variable for accelerometer error scaling.
    [config.cpp]
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2023-05-02 User newer version of clang (15) and fix errrors.
    [afro_esc.cpp, i2c_conn.cpp, main.cpp]
2023-08-06 Align code with new T-MOTOR brushless motors.
    [tmotor_mn2212_9p5x4p5.json]
